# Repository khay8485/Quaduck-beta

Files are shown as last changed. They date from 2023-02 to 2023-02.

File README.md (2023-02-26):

# Quaduck

Hello dear friend of excentric 3D-printers, may I introduce the Quaduck, 
an IDEX Printer with in Z completely independent Toolheads, based on the Voron Switchwire.
The naming originates from a long CAD session, where I started seeing a duck's face on a 
specific part of the printer. Therefore Switchwire meets ZIDEX meets ducks.

The files contain the first version of an assembly manual, but it is missing steps that 
are unchanged from SW or discovered after writing.

CAD is included hence beta, cause other projects needed the data.
Be aware, that I am NOT maintaining this repo on a daily basis, so it might be outdated. 

If you have questions, feel free to ask on discord. Add an # between my github-username.

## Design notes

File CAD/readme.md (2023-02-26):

CAD Version 42, no history but hidden parts of SW-origin

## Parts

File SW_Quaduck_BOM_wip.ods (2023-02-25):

Category | Part | Quantity | Quantity for Quaduck
Frame | 3060 Extrusion – 520mm | 2 | 2
 | 3030 Extrusion – 300mm | 2 | 2
 | 3030 Extrusion – 360mm | 1 | 1
 | 3030 Extrusion – 400mm | 2 | 2
 | 2020 Extrusion – 340mm | 2 | 3
Fasteners | M3 Threaded Insert | 54 | 40
 | M3 T-Nut (For 2020) | 13 | 28
 | M3 T-Nut (For 3030) | 12 | 24
 | M5 T-Nut (For 2020) | 12 | 15
 | M5 T-Nut (For 3030) | 55 | 42
Bearringstacks | M5 1mm Spacer | 19 | 42
TAP Rail | M3 Hexnut | 3 | 4
Frame | M8x16 BHCS | 8 | 8
XZ-Idlers | M5x50 BHCS |  | 4
Keybak, | M5x40 SHCS | 6 | 2
Y-Idler, Xz-blocks, | M5x30 BHCS | 5 | 9
Feet, XZ-Motormounts, | M5x16 BHCS | 12 | 12
Railstopper, XZ-Idler, PDU, Y-Idler, Y-Motor, Deckpanel, YZ-Chainholder, Skirts, XZ-Blocks | M5x10 BHCS | 50 | 40
PDU | M4x8 BHCS | 4 | 3
XZ-Motormounts, | M3x40 SHCS | 7 | 4
XZ-Idlers, Y-Motor, Beplate, E-Fans, XZ-Motormounts | M3x30 SHCS | 28 | 30
 | M3x25 SHCS | 2
 | M3x20 SHCS | 3
 | M3x16 SHCS | 12
Y-Beltholder, | M3x12 SHCS | 12 | 1
Rails, Bedplate, Skirts, X-Cablecover, XZ-Blocks | M3x8 SHCS | 66 | 88
 | M3x6 FHCS | 9
Y-Endstop, X-Endstop | M2x10 Self-tapping Screw | 8 | 6
Bed Fasteners | M3x12 FHCS (SS) | 9 | 9
 | 6x6x3mm Spacer (SS) | 9 | 9
Vibration Management | Rubber Compressor Foot | 4 | 4
Motion | MGN12H Linear Rail – 300mm | 4 | 7
 | GT2 20T Pulley (5mm B, 6mm W) | 3 | 5
 | GT2 Belt (6mm W) - 1500mm | 2 | 4
 | GT2 Belt (6mm W) - 800mm | 1 | 1
 | F695 Bearing | 20 | 42
 | BMG Extruder Components Kit | 1 | 2
Electronics | NEMA17 Motor 17HS15-1504S1 | 3 | 5
 | SPDT KW10 Limit Micro Switch | 2 | 4
 | Omron TL-Q5MC2 - NPN Inductive Probe | 1 | 0
 | Hotend Kit (24V) | 1 | 2
 | 2020 Extrusion – 340mm | 1 | 1-2
 | 40x40x10 Axial Fan (24V) | 1 | 2
 | Moons CSE14HRA1L410A-01 |  | 2
 | Mini 12864 Display | 1 | optional
 | Inlet Power Socket IEC320 C14 | 1 | 1
 | Keystone CAT6 Insert | 1 | optional
 | BTT Octopus with 7 Drivers |  | 1
 | 60x60x20 Axial Fan (24V) | 1 | optional
 | USB Cable A-male B-male | 2
 | RaspberryPi3 B+ | 1 | 1
 | Mean Well LRS-350-24 PSU | 1 | 1
 | Mean Well RS-25-5 PSU | 1 | 0
 | BAT85 Diode | 1 | 0
 | C13 Power Cord | 1 | 1
 | MOSFET Trigger Switch Drive Module | 2 | optional
 | LED Strip 240mm 24v | 2 | optional
Buildplate | Prusa MK3 Y Carrier | 1 | 1
 | Prusa MK52 Heated Bed - 24V | 1 | 1
 | Spring Steel Sheet for Prusa MK52 Bed | 1 | 1
Misc | Key-Bak Super 48 Retractable Keychain | 1 | 2
 | 3M VHB Tape 5952 | 1
 | Loctite Blue Threadlocker Stick | 1
 | 6x3mm Neodymium Magnet | 8 | 4
 | PTFE Tube (4mm OD 2mm ID) - 300mm | 1
Cable Management | 10x11 Cable Chain | 3 | 5
Cables | 16AWG PTFE Cable (10ft total) | 1
 | 20AWG PVC Cable (10ft total) | 1
 | 24AWG PTFE Cable (100ft total) | 1
Panels | 366x270x3 Coroplast Panel | 1
 | 441x270x3 Coroplast Panel | 2
 | 426x360x3 Coroplast Panel | 2
 | 478x170x3 Coroplast Panel | 2
 | 478x360x3 Coroplast Panel | 2
 | 433x183x3 Acrylic Panel | 2
 | 366x250x3 Acrylic Panel | 1
 | 441x250x3 Acrylic Panel | 2

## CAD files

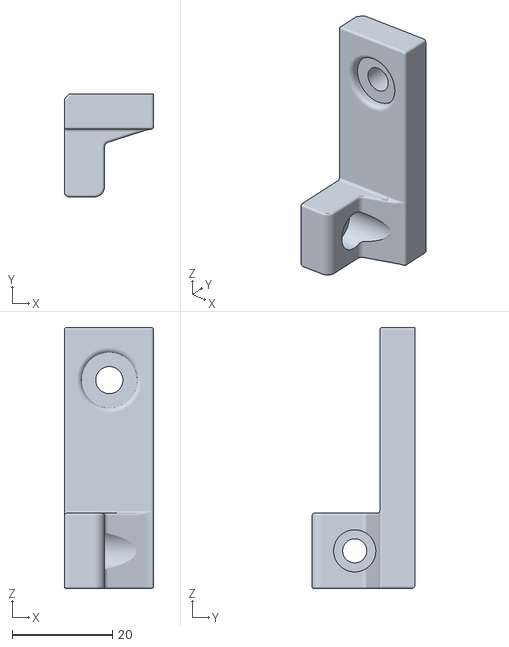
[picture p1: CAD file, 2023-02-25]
Electronics/PS_2020_Mount_M4x6.stl
17.8 x 20.5 x 52.0

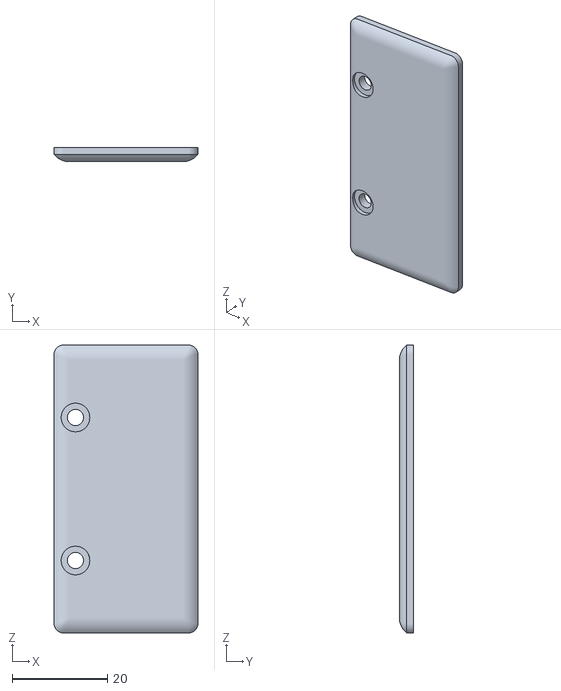
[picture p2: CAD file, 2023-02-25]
Skirts/endcapducky_mmu.stl
30.2 x 3.00 x 60.4

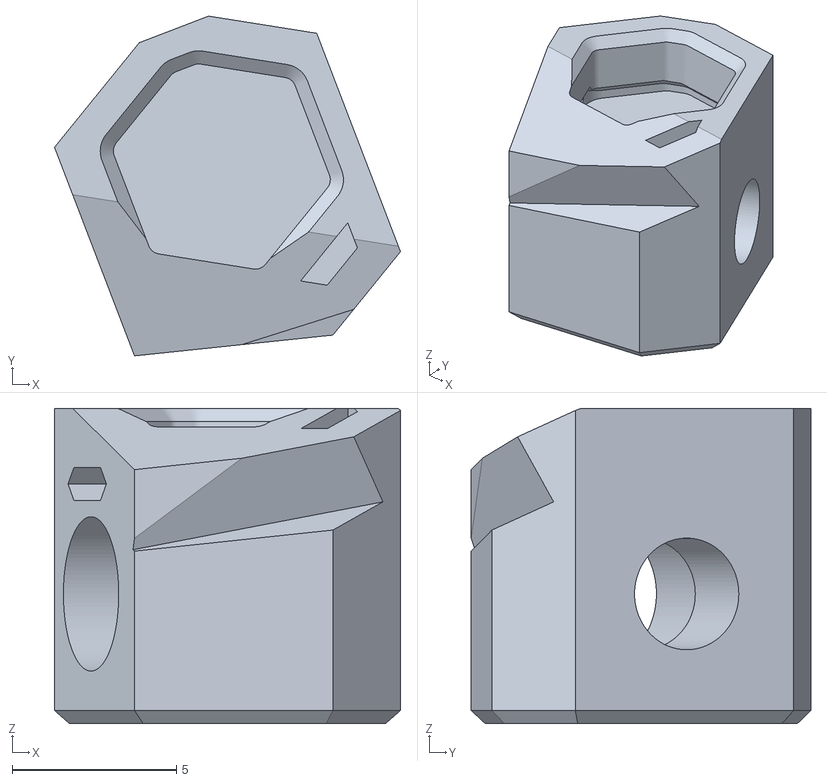
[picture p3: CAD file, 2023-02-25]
x2/Carriage/tippi_mag_right.stl
10.5 x 10.3 x 9.60

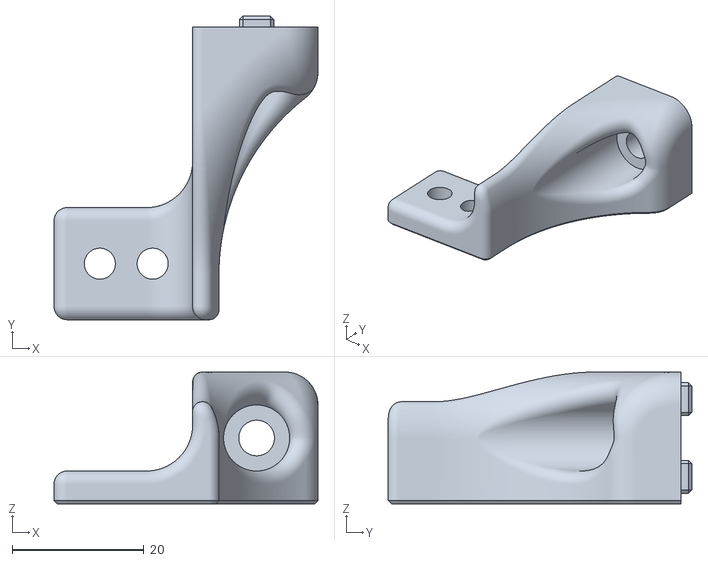
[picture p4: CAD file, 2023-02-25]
x2/X-Axis/z_chain_x_mount.stl
40.0 x 46.0 x 20.0

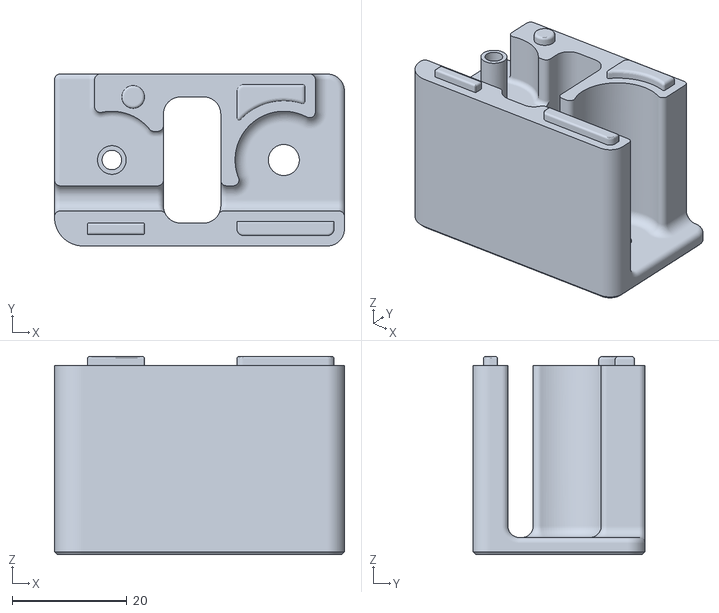
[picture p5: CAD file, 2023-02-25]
x2/XZ-System/upper_idler_right_a.stl
50.6 x 30.0 x 34.6

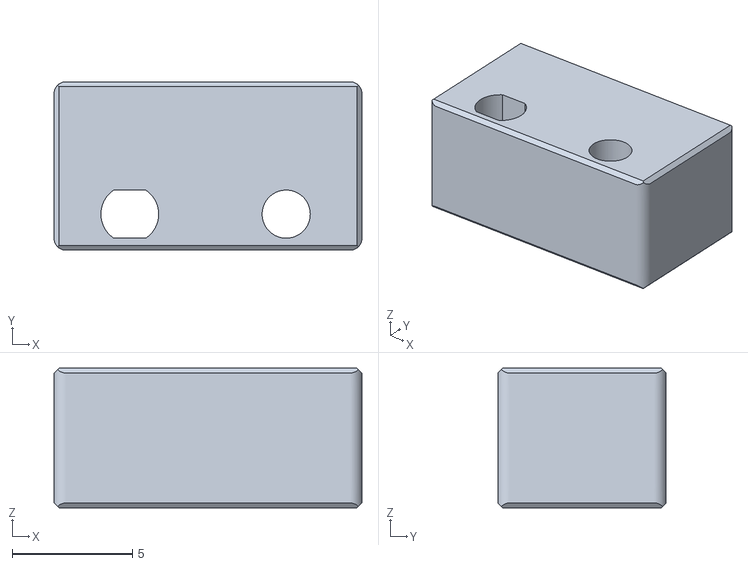
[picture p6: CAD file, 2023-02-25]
Y-Axis/[a]_dummy_microswitch.stl
12.8 x 7.00 x 5.80

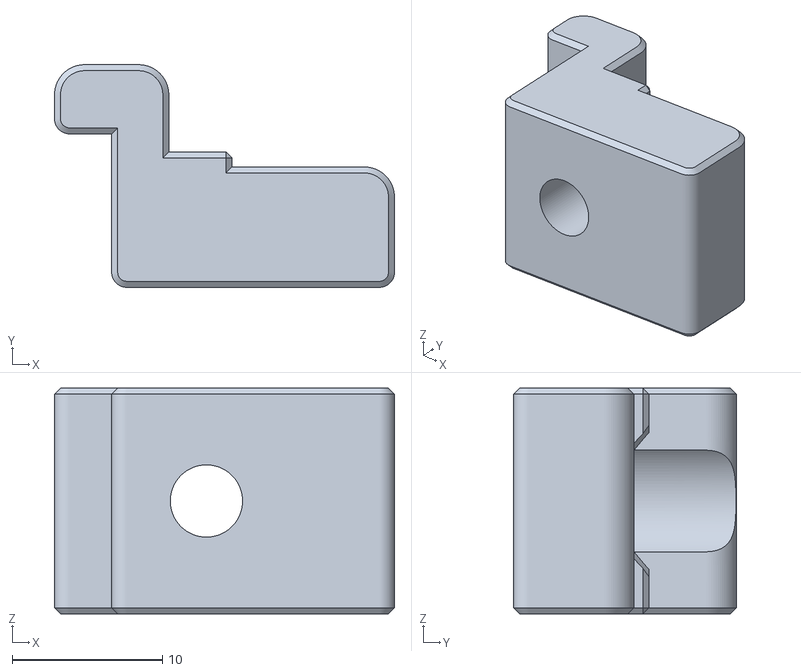
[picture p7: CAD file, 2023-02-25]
Electronics/PS_3030_Mount_x2.stl
22.6 x 14.8 x 15.0

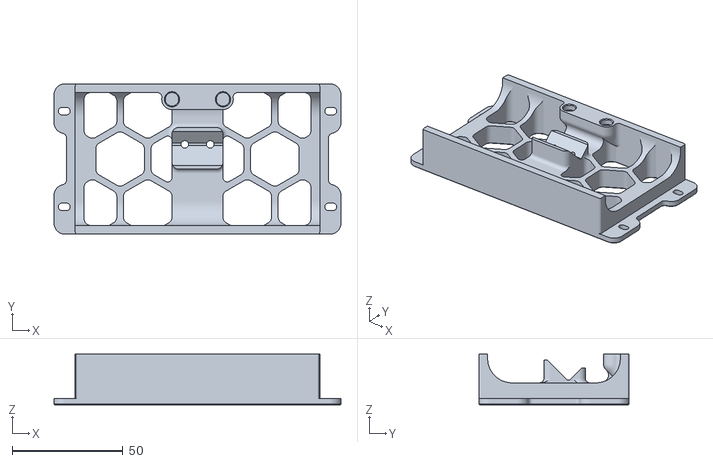
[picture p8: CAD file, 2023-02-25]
Skirts/grill_front_middle.stl
129.8 x 68.0 x 23.0

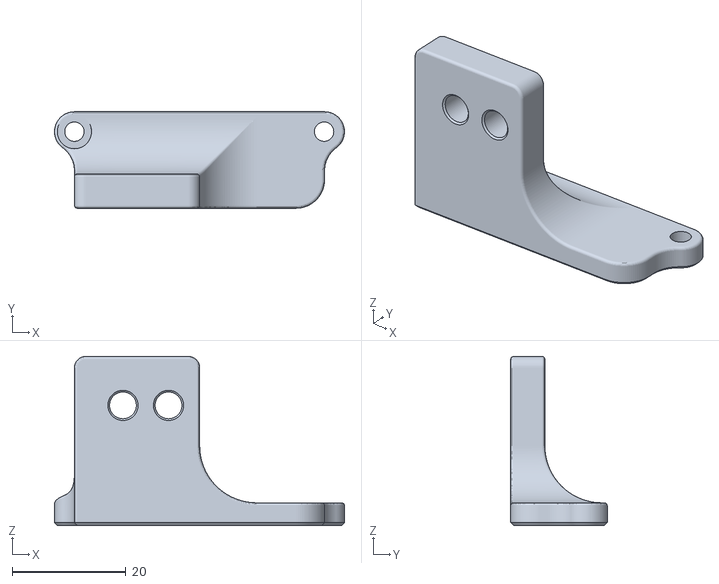
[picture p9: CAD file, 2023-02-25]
x2/Carriage/x_carriage_chainmount_rev1.stl
50.9 x 16.9 x 29.7

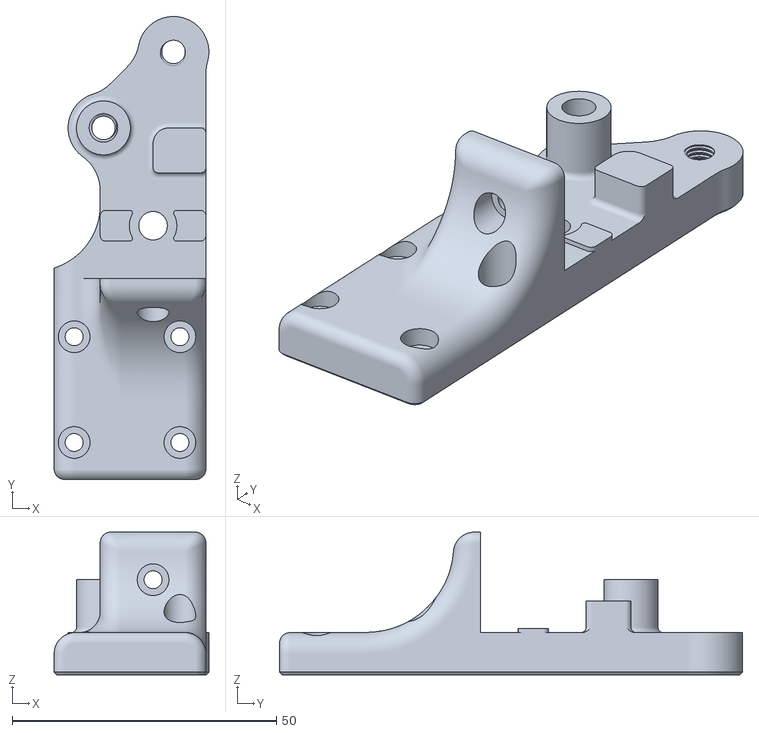
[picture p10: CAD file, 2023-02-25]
x2/X-Axis/(a) xz_block_right_ducky_V2.stl
29.3 x 87.6 x 27.0

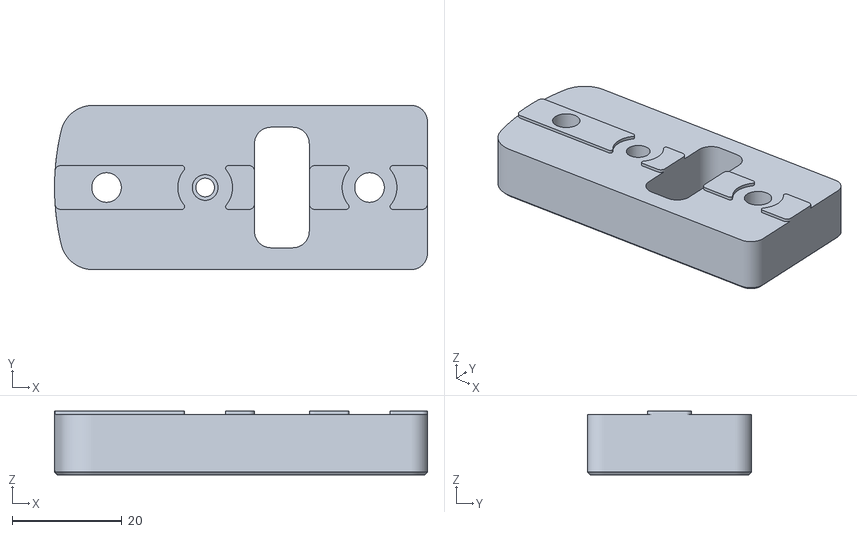
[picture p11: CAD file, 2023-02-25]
x2/XZ-System/(a) upper_idler_right_b.stl
68.1 x 30.0 x 11.6

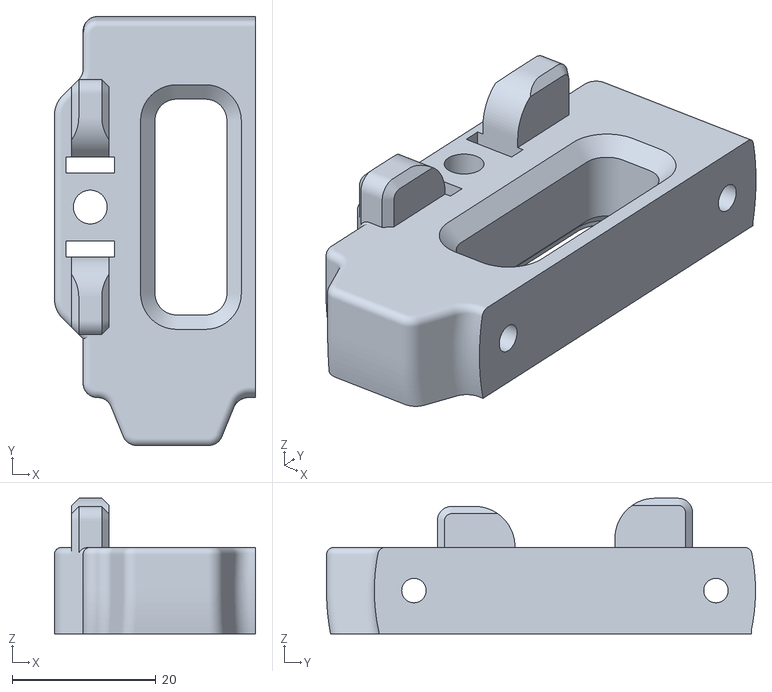
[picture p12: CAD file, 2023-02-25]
Y-Axis/y_belt_anchor_sensorless.stl
28.0 x 59.7 x 18.8

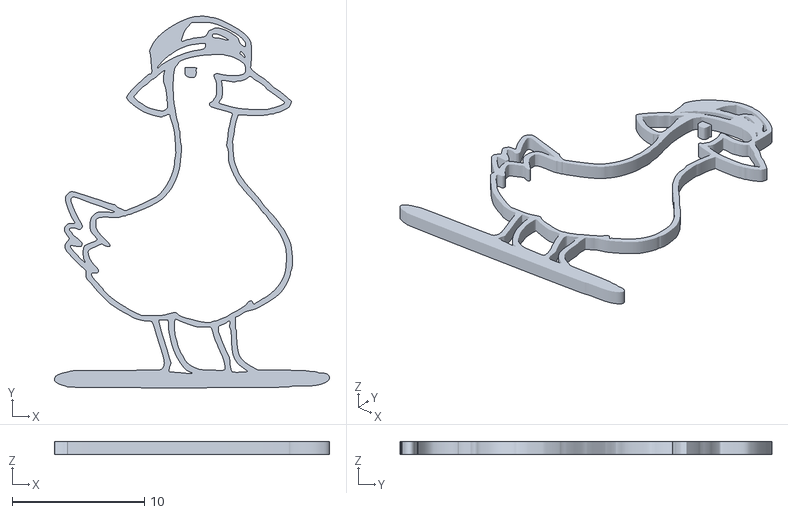
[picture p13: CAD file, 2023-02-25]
Skirts/endcapducky_single.stl
20.8 x 28.1 x 1.00

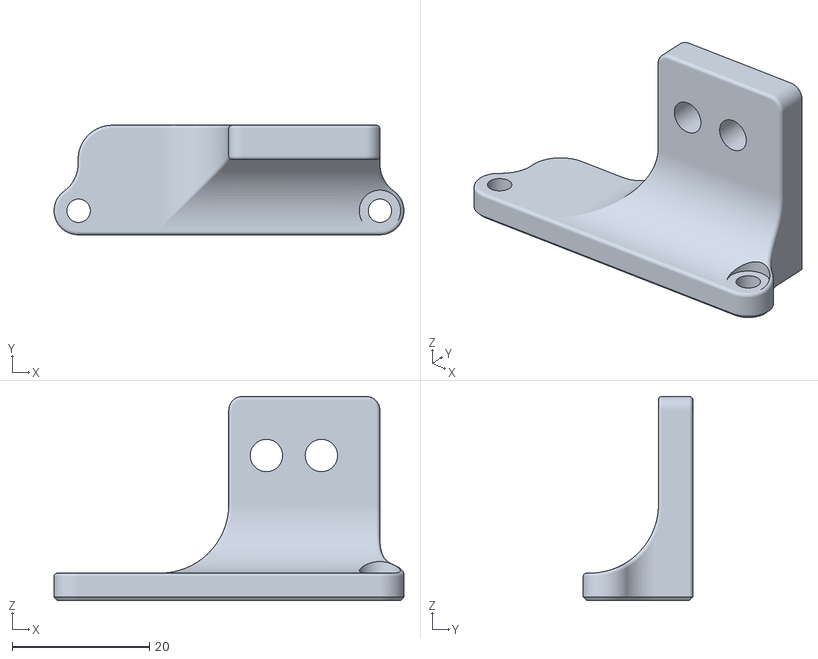
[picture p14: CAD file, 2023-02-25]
x2/Carriage/x_carriage_chainmount.stl
50.9 x 15.9 x 29.7

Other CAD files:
Electronics/PS_2020_Mount.stl
x2/X-Axis/xz_block_left_front.stl
x2/XZ-System/x_motor_mount_a.stl
Y-Axis/y_idler_upper.stl
Electronics/PS_3030_Mount_M4x6 x2.stl
Electronics/octopus_mount.stl
Electronics/raspberry_pi_mount.stl
Skirts/12mm printed spacer x2-4.stl
Skirts/[a]_grill_endcap_d_x2.stl
Skirts/[a]_grill_endcap_x2.stl
Skirts/grill_front_x2.stl
Skirts/grill_rear_left_inlet.stl
Skirts/grill_rear_middle.stl
Skirts/grill_rear_right.stl
Y-Axis/(a) zy_chain_frame_mount_x2.stl
Y-Axis/[a]_y_belt_clip.stl
Y-Axis/[a]_y_chain_bed_mount_generic.stl
Y-Axis/[a]_y_chain_bed_mount_igus.stl
Y-Axis/heatbed_terminals_cover.stl
Y-Axis/y_belt_anchor.stl
Y-Axis/y_carriage_drill_guide.stl
Y-Axis/y_idler_lower.stl
Y-Axis/y_motor_mount_a.stl
Y-Axis/y_motor_mount_b.stl
x2/Carriage/(a) xz_belt_clip_x2.stl
x2/Carriage/sb_strain_relief_spacer_x2.stl
x2/Carriage/tippi_mag_left.stl
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

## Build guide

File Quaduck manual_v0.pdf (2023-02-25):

# Quaduck

## Voron Switchwire Double X-Gantry Version/Mod

### Hello dear friend of excentric 3D-printers, may I introduce the Quaduck, an IDEX Printer with in Z completely independent

Toolheads, based on the Voron Switchwire.

### The naming originates from a long CAD session, where I started seeing a duck's face on a specific part of the printer. Can you see it? Well, then you have to build it. ;-)

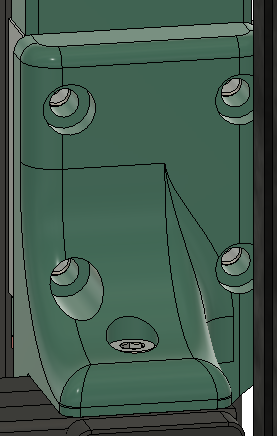
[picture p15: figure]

### nat nat

### It combines: - ZIDEX 3D-Printer idea - Switchwire - TAP - Mini Stealthburner - Ducks

## XZ-Motionsystem

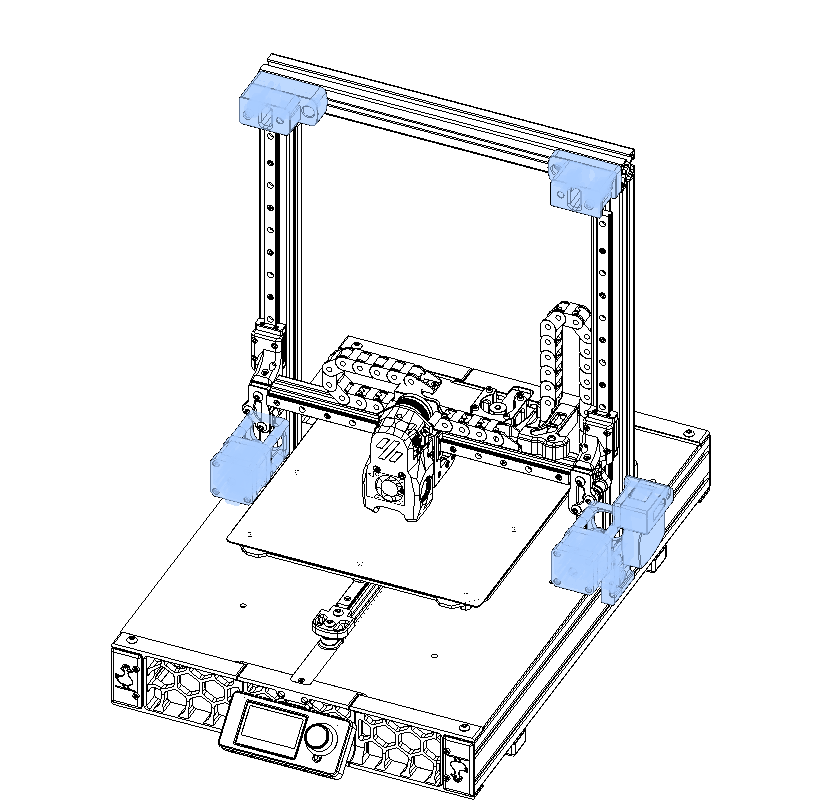
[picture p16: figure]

Rudimentary Build Manual for Tool0-Side of the Duck.

### You will the printed parts from: - X2 / XZ-System

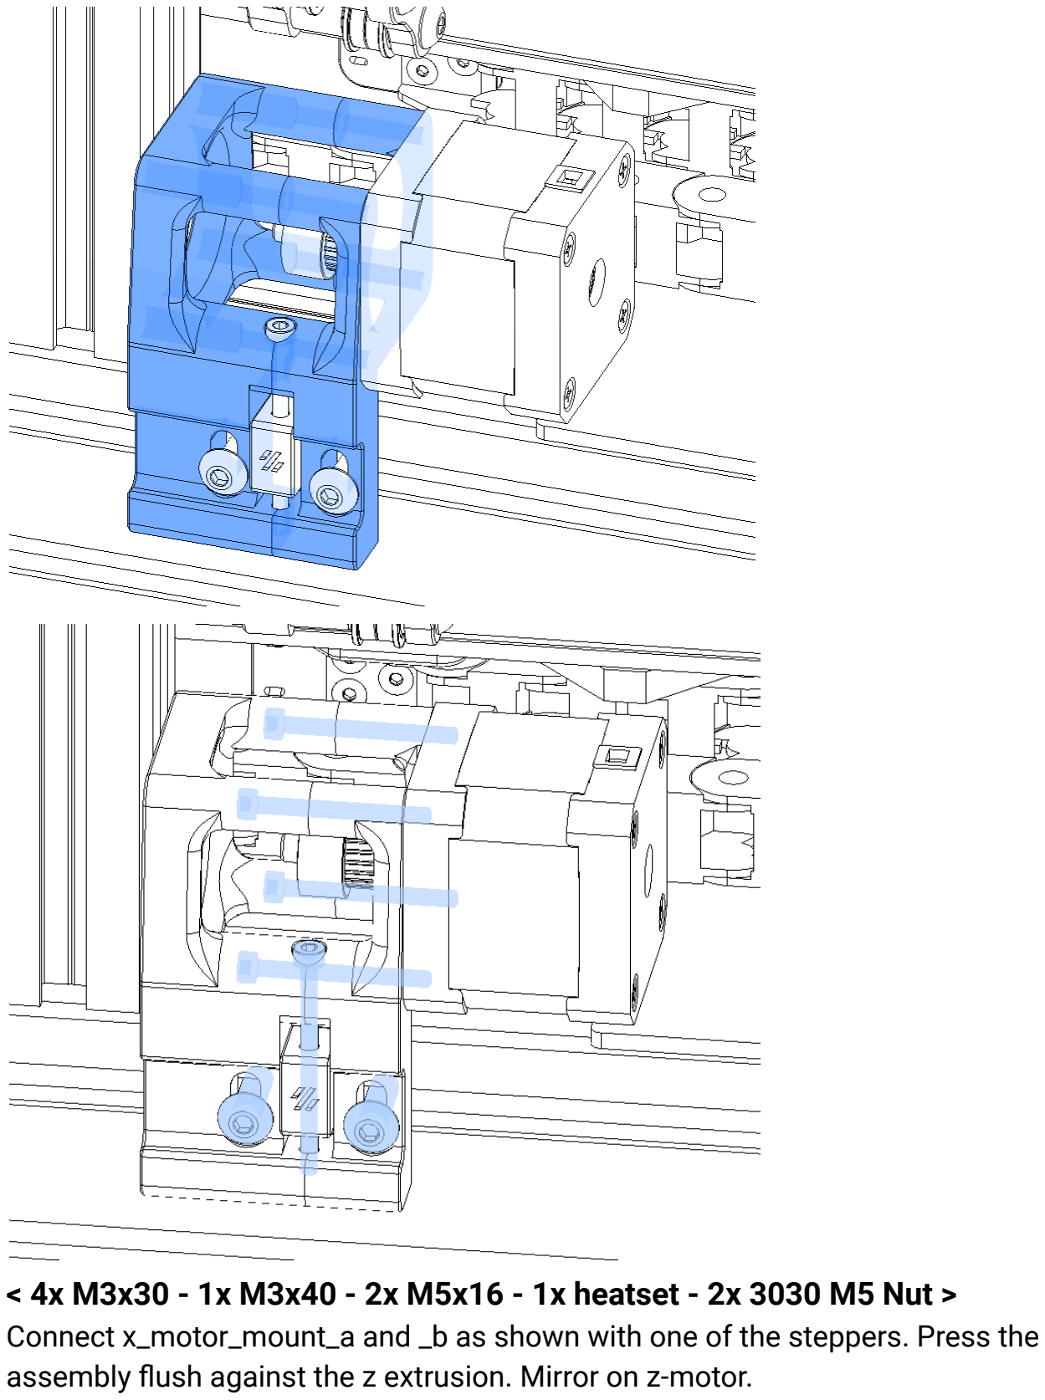
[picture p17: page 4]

< 4x M3x30 - 1x M3x40 - 2x M5x16 - 1x heatset - 2x 3030 M5 Nut > Connect x_motor_mount_a and _b as shown with one of the steppers. Press the assembly flush against the z extrusion. Mirror on z-motor.

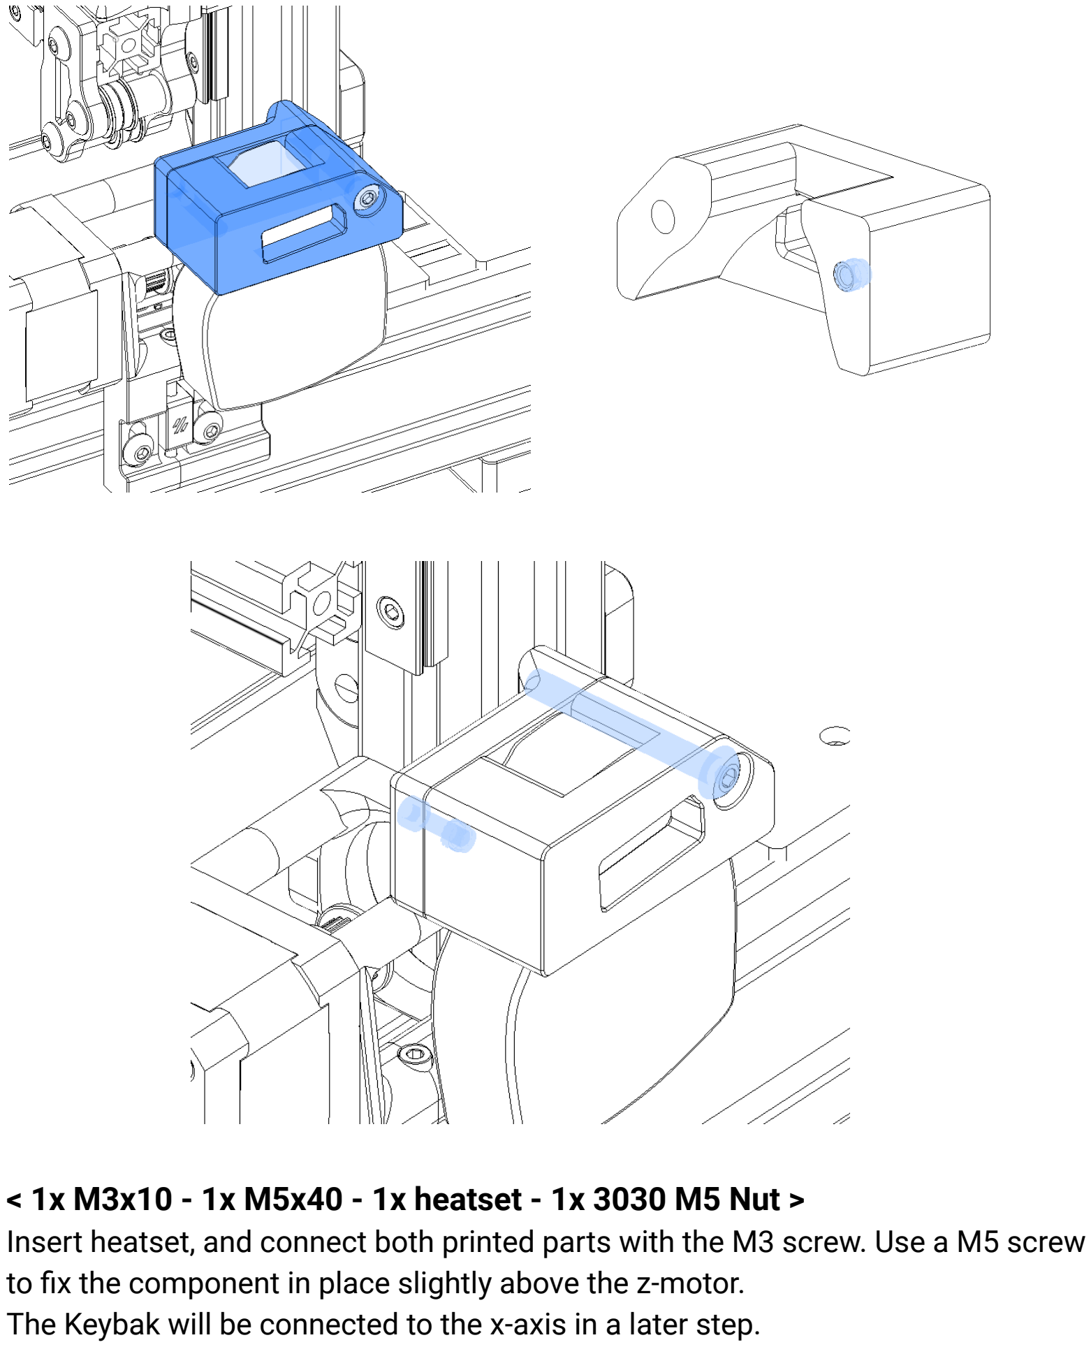
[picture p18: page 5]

< 1x M3x10 - 1x M5x40 - 1x heatset - 1x 3030 M5 Nut >
Insert heatset, and connect both printed parts with the M3 screw. Use a M5 screw to fix the component in place slightly above the z-motor.
The Keybak will be connected to the x-axis in a later step.

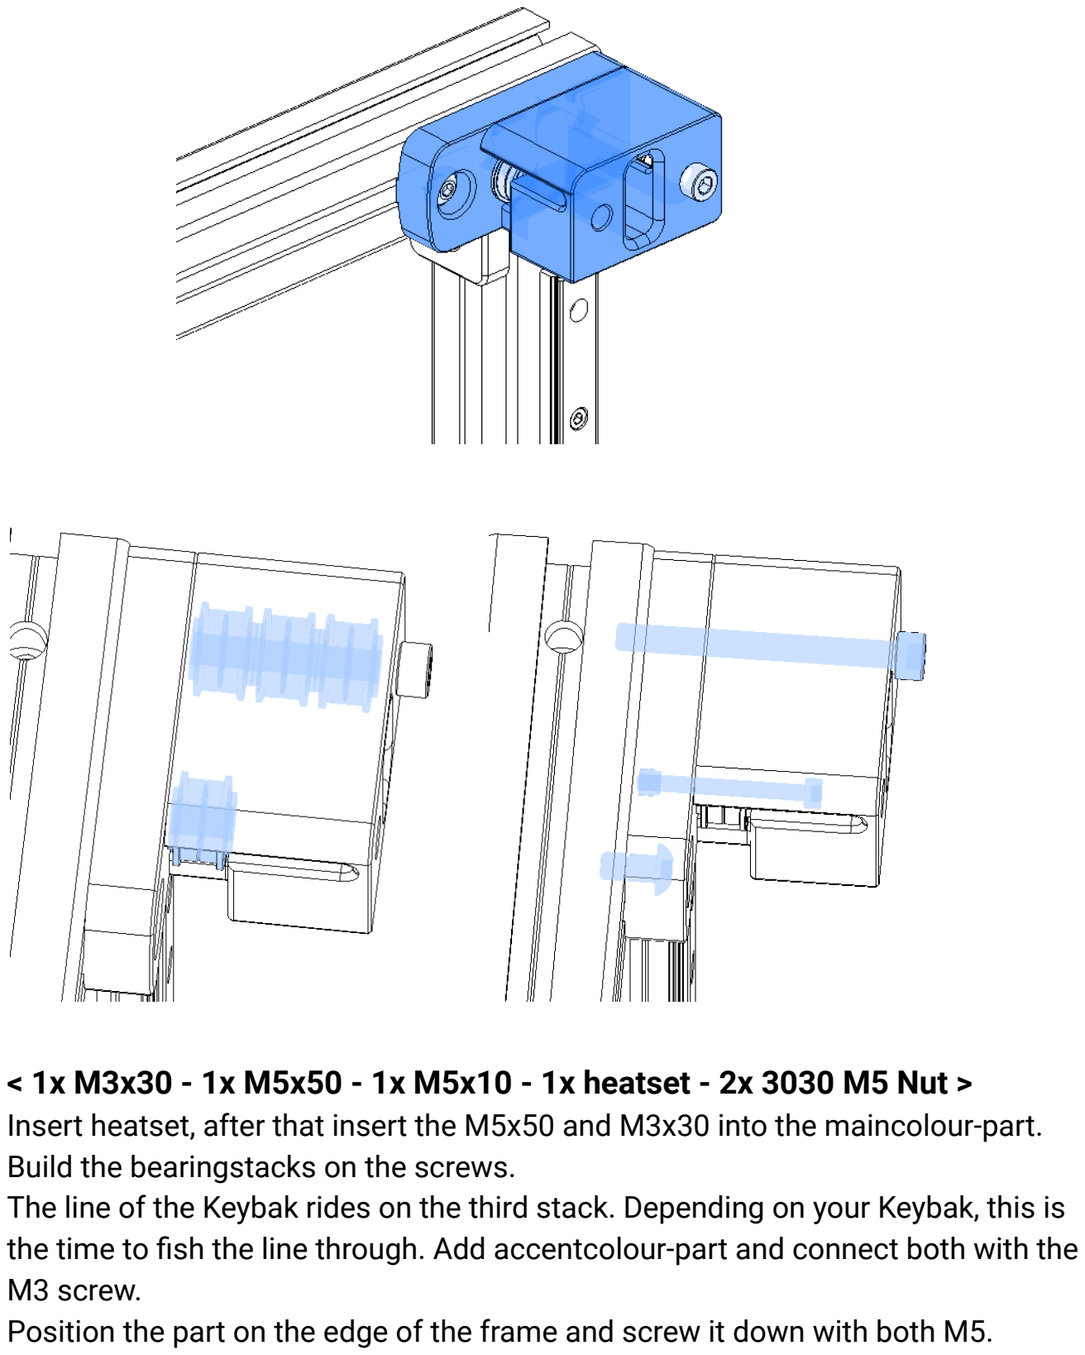
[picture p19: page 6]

< 1x M3x30 - 1x M5x50 - 1x M5x10 - 1x heatset - 2x 3030 M5 Nut > Insert heatset, after that insert the M5x50 and M3x30 into the maincolour-part. Build the bearingstacks on the screws.
The line of the Keybak rides on the third stack. Depending on your Keybak, this is the time to fish the line through. Add accentcolour-part and connect both with the M3 screw.
Position the part on the edge of the frame and screw it down with both M5.

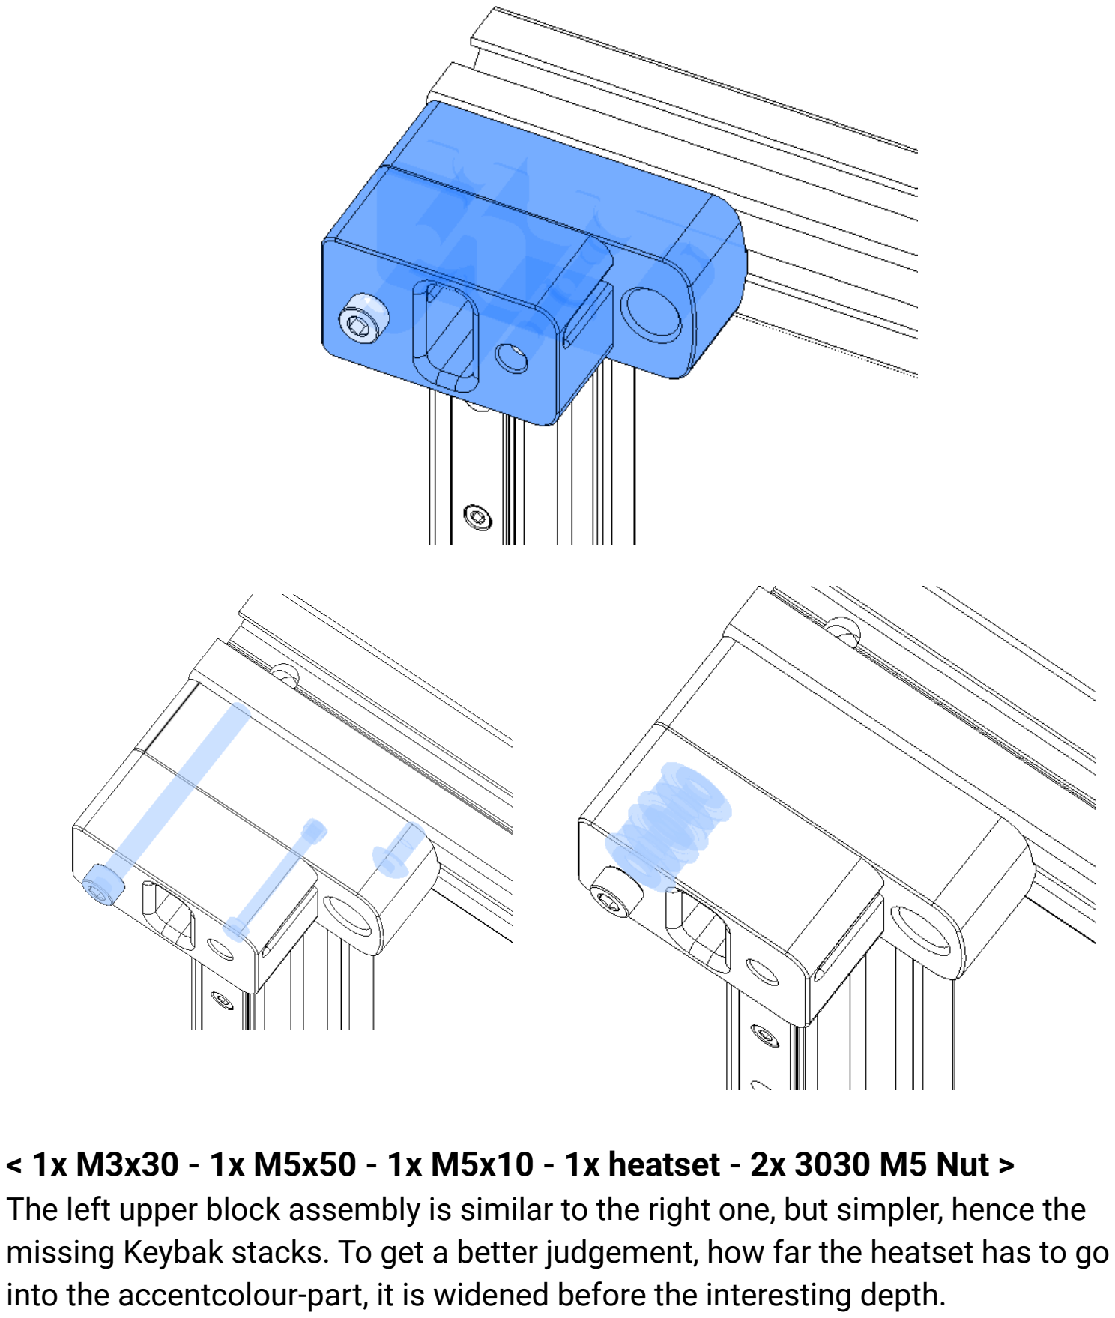
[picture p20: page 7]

< 1x M3x30 - 1x M5x50 - 1x M5x10 - 1x heatset - 2x 3030 M5 Nut >
The left upper block assembly is similar to the right one, but simpler, hence the missing Keybak stacks. To get a better judgement, how far the heatset has to go into the accentcolour-part, it is widened before the interesting depth.

## X-Carrier - TAP - Toolhead

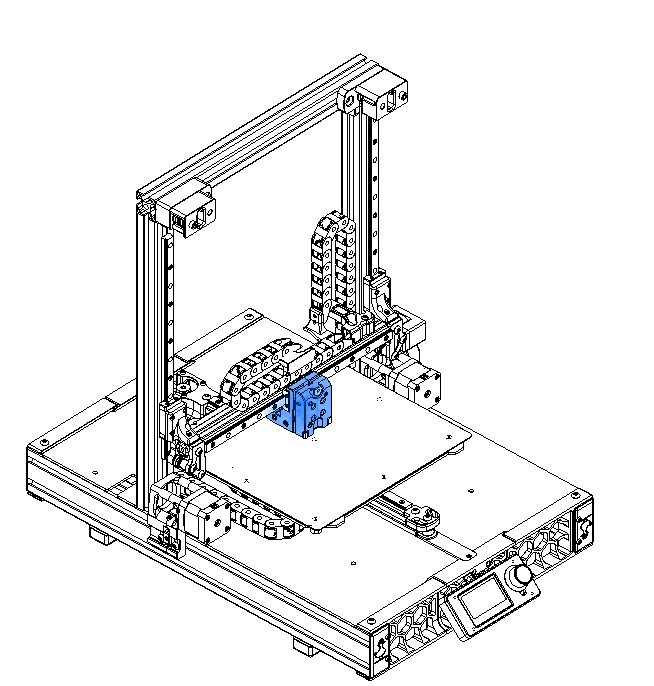
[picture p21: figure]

### You will the printed parts from: - X2 / Carriage

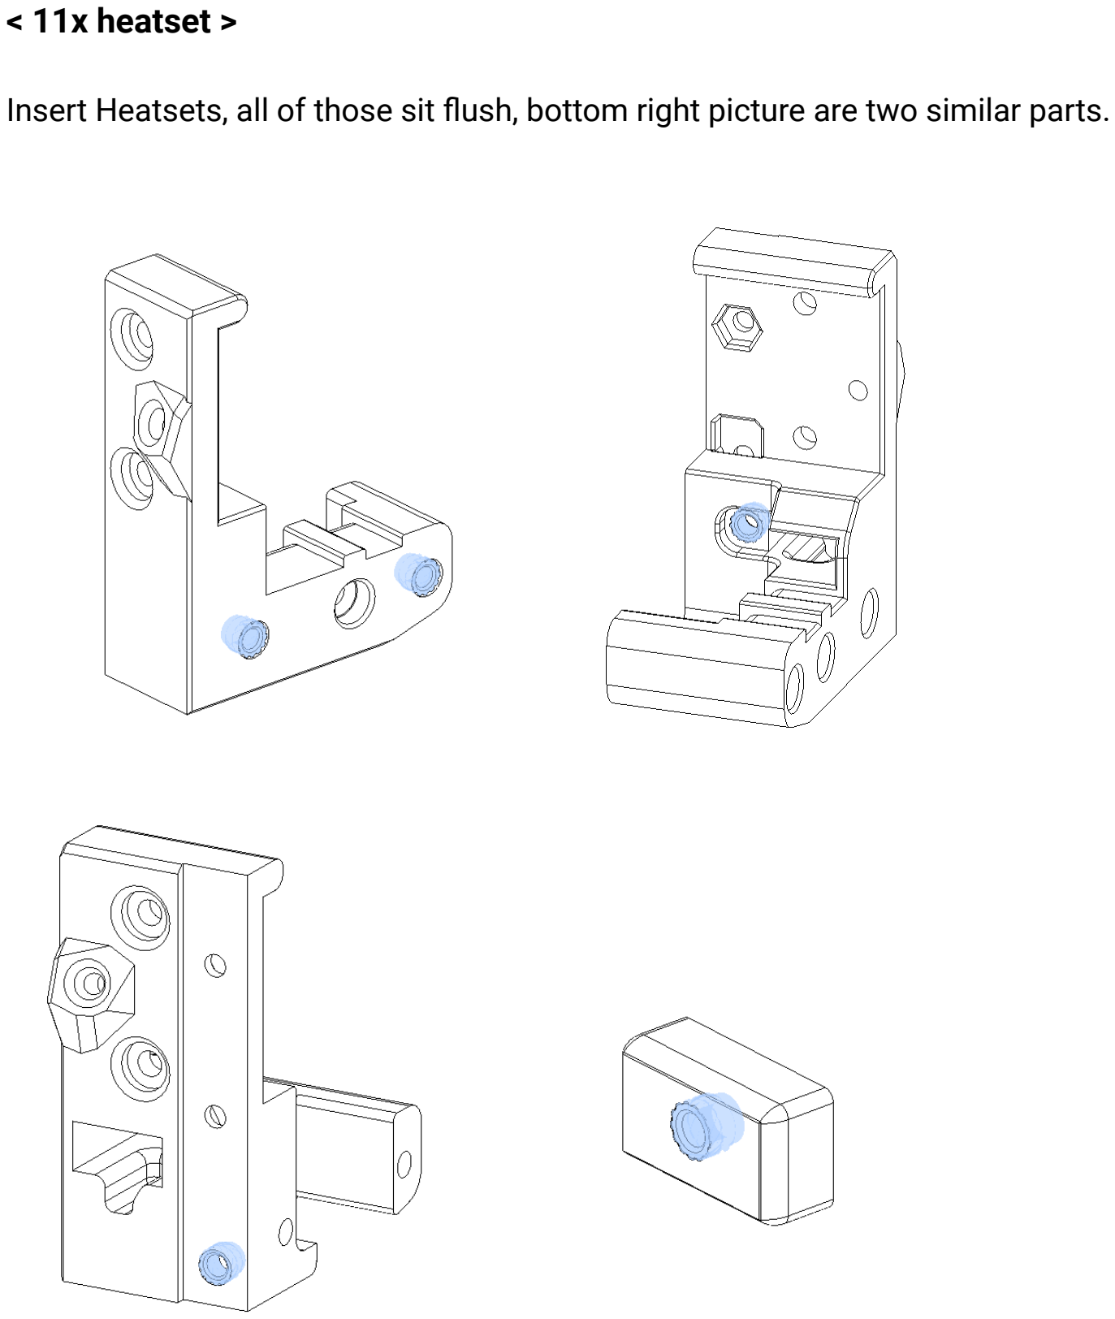
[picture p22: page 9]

< 11x heatset >

Insert Heatsets, all of those sit flush, bottom right picture are two similar parts.

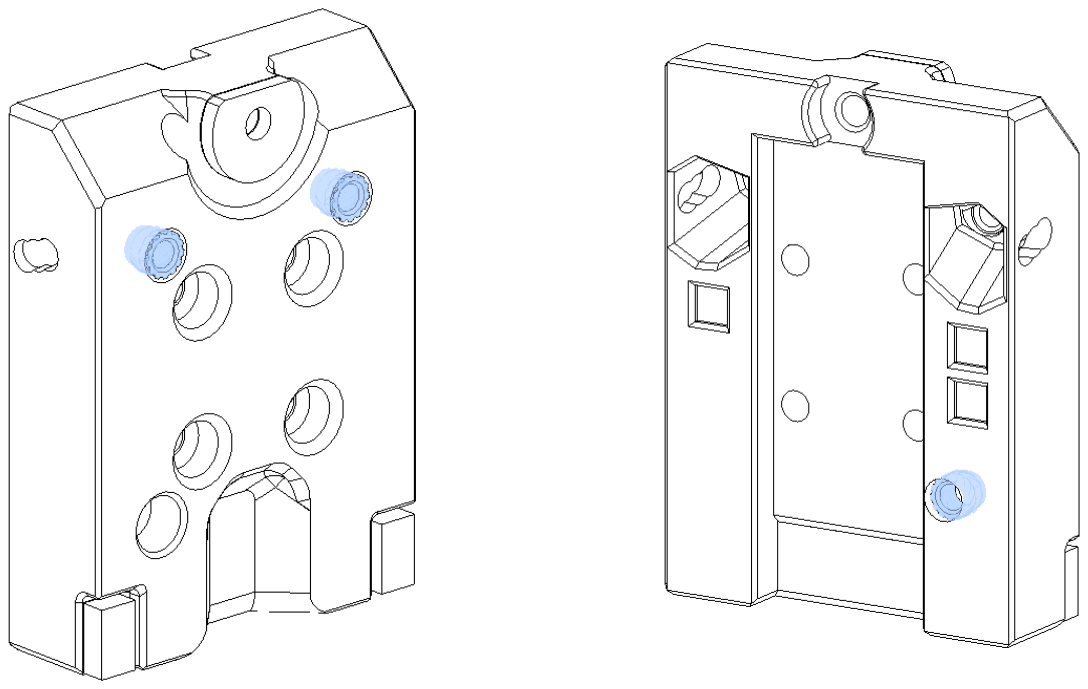
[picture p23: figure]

You can remove the build in supports on this part, maybe the round one needs some conviction with a small flathead screwdriver.

Not shown: the two magnet holder pieces, which each get a heatset too.

< 2x M3x40 - 1x M3x6 - 2x M3 Hex nuts >
Connect both parts and insert the Hex nuts. Add the wired TAP-Sensor.
If you have one with Screw-Terminals on both side, use your flush cutter to get rid of one.

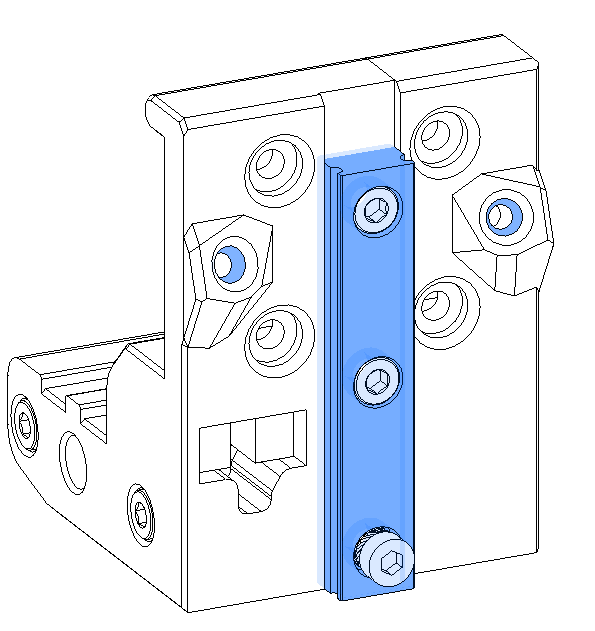
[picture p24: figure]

< 2x M3x6 FHCS - 2x M3x6 - 1x M3x12 - 1x heatset >
Screw the magnetic M3x6 into the elevated parts. Add the TAP MGN9 Rail, use a heatset on the lowest screw. It is a third restingpoint for the toolhead.

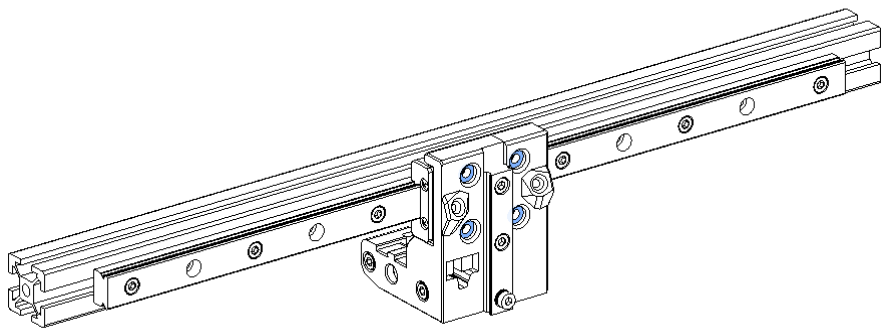
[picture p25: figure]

< 4x M3x8 BHCS >
At this point, you need to mount the carriage onto the x-rail. The handling of this situation will get a bit tricky.

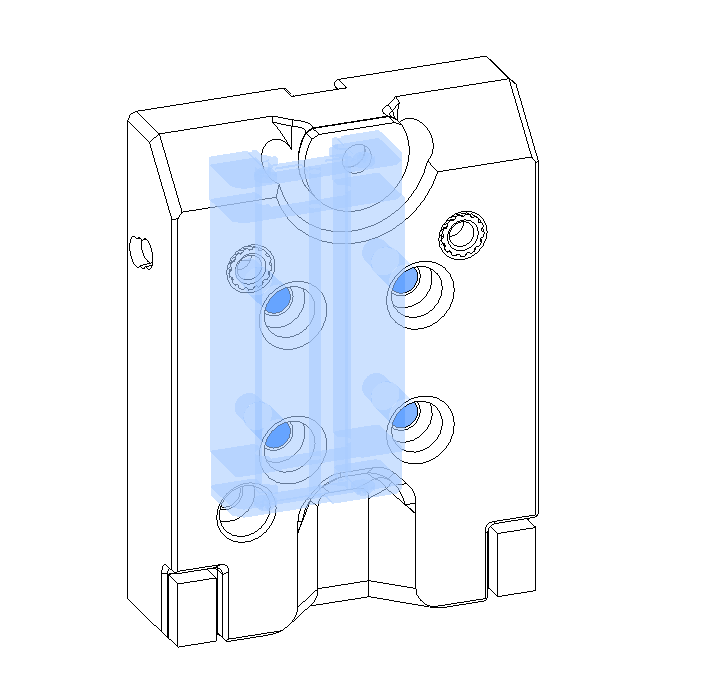
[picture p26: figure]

< 4x M3x8 >
Screw the TAP MGN9 block to the carriage front. Extreme caution when handling this part in the future, as those little balls can get lost easily.

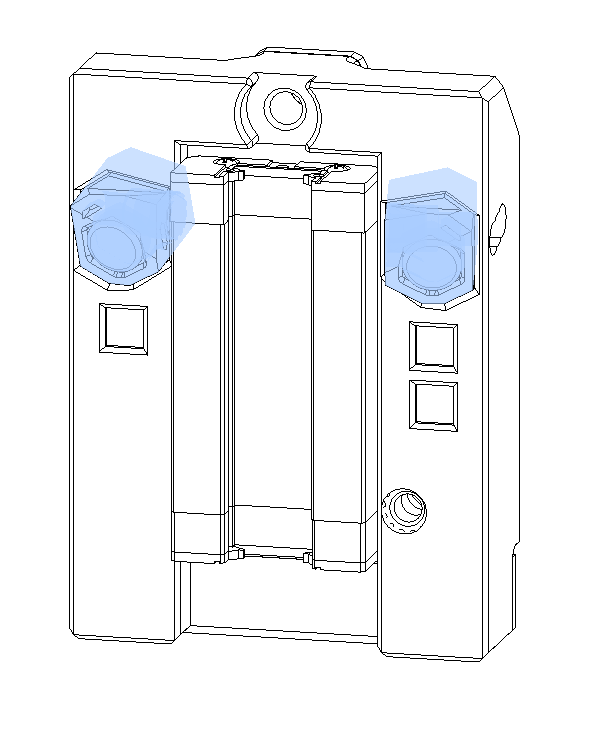
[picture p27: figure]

< 2x M3x10 BHCS - 2 M3 washer >
The magnet holder thingies are marked with dots, the part has similar markings to help you find the right spot for them. Push them all the way in, check loose fit and tack them lightly in place with the screws.

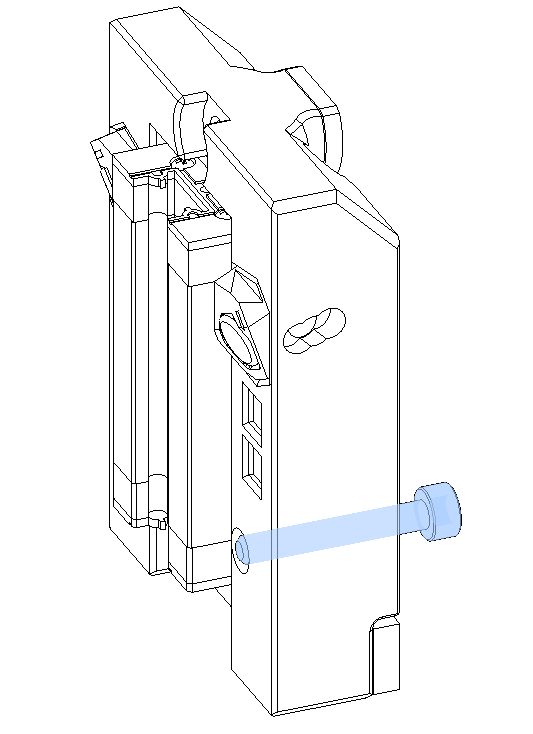
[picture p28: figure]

< 1x M3x20 >
Add the M3x20 as shown. Don’t overshoot the part! This screw will be the trigger for the TAP-Sensor.

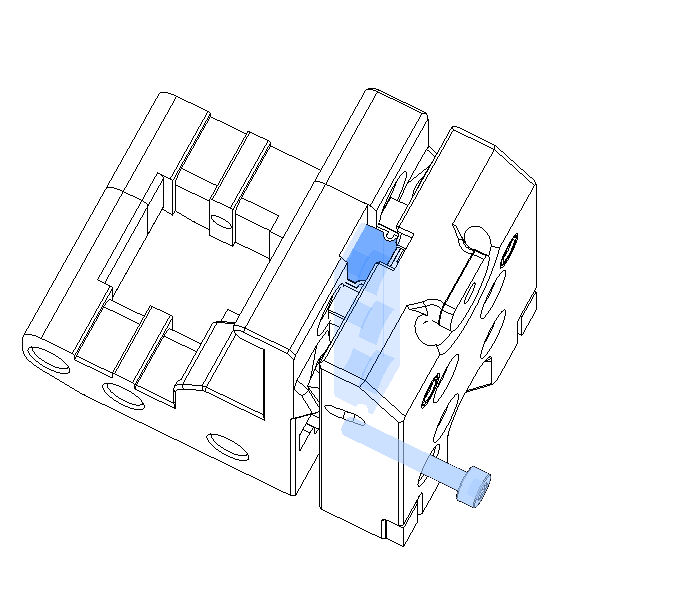
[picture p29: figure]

Gently slide the Carriage front on the MGN9 TAP-Rail. Be cautious, you don’t want to lose any balls out of the block. Slide it all the way down and hold the parts tight in one hand. Screw the M3x20 all the way in. The screw will make sure the carriage-front will not fall off.

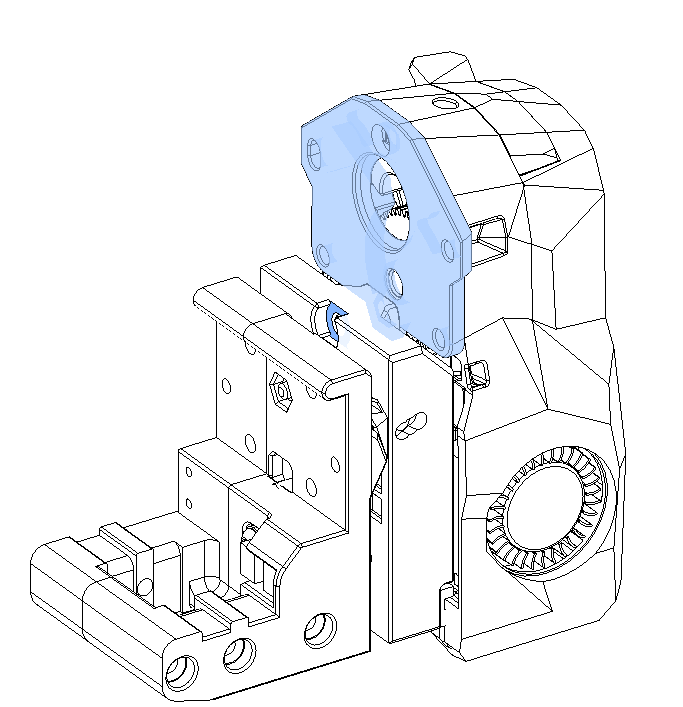
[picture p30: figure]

< 1x M3x12 - 2x M3x35 >
Build the Mini SB Toolhead to the part where you would add the motor. At this stage, connect the Toolhead to the carriage. It will get screwed in on three different spots. To reach the marked one on the picture, gently push up the carriage front. The other two are screwed in from the front.

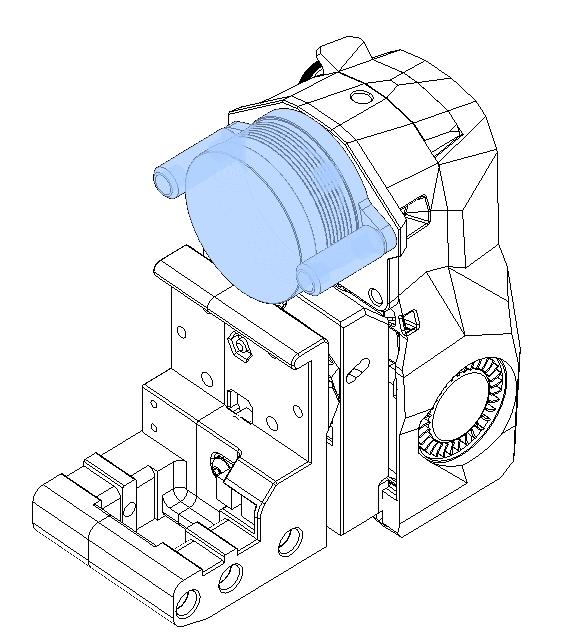
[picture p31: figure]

< 2x M3x10 - 4x heatsets >
Add the stepper motor and strain relief spacers as stated in the Mini-SB manual.

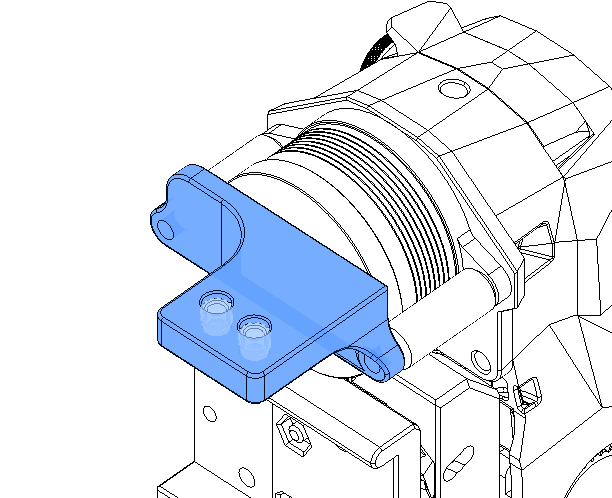
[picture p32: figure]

< 2x M3x8 - 2x heatsets >
The last part is the carriage chainmount. It has another two heatsets and gets screwed in place with two M3x8s.

## X-Axis & more Chainmounts

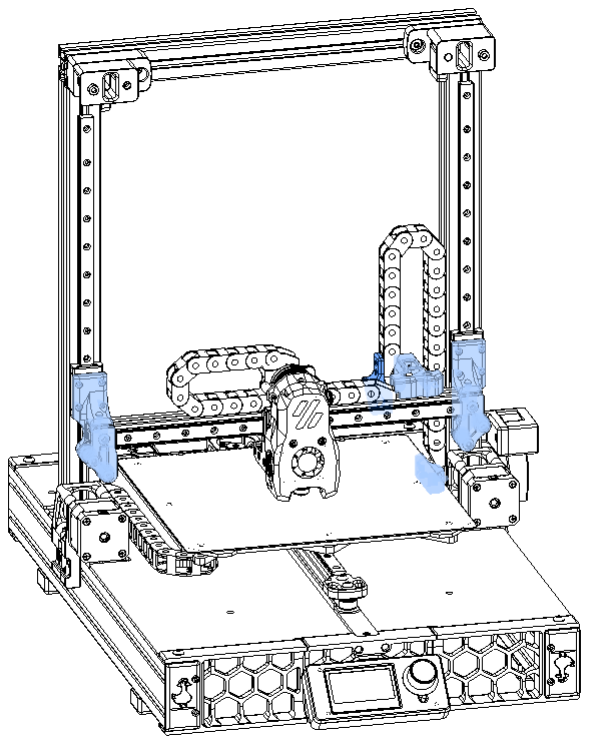
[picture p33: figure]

### You will the printed parts from: - X2 / X-Axis

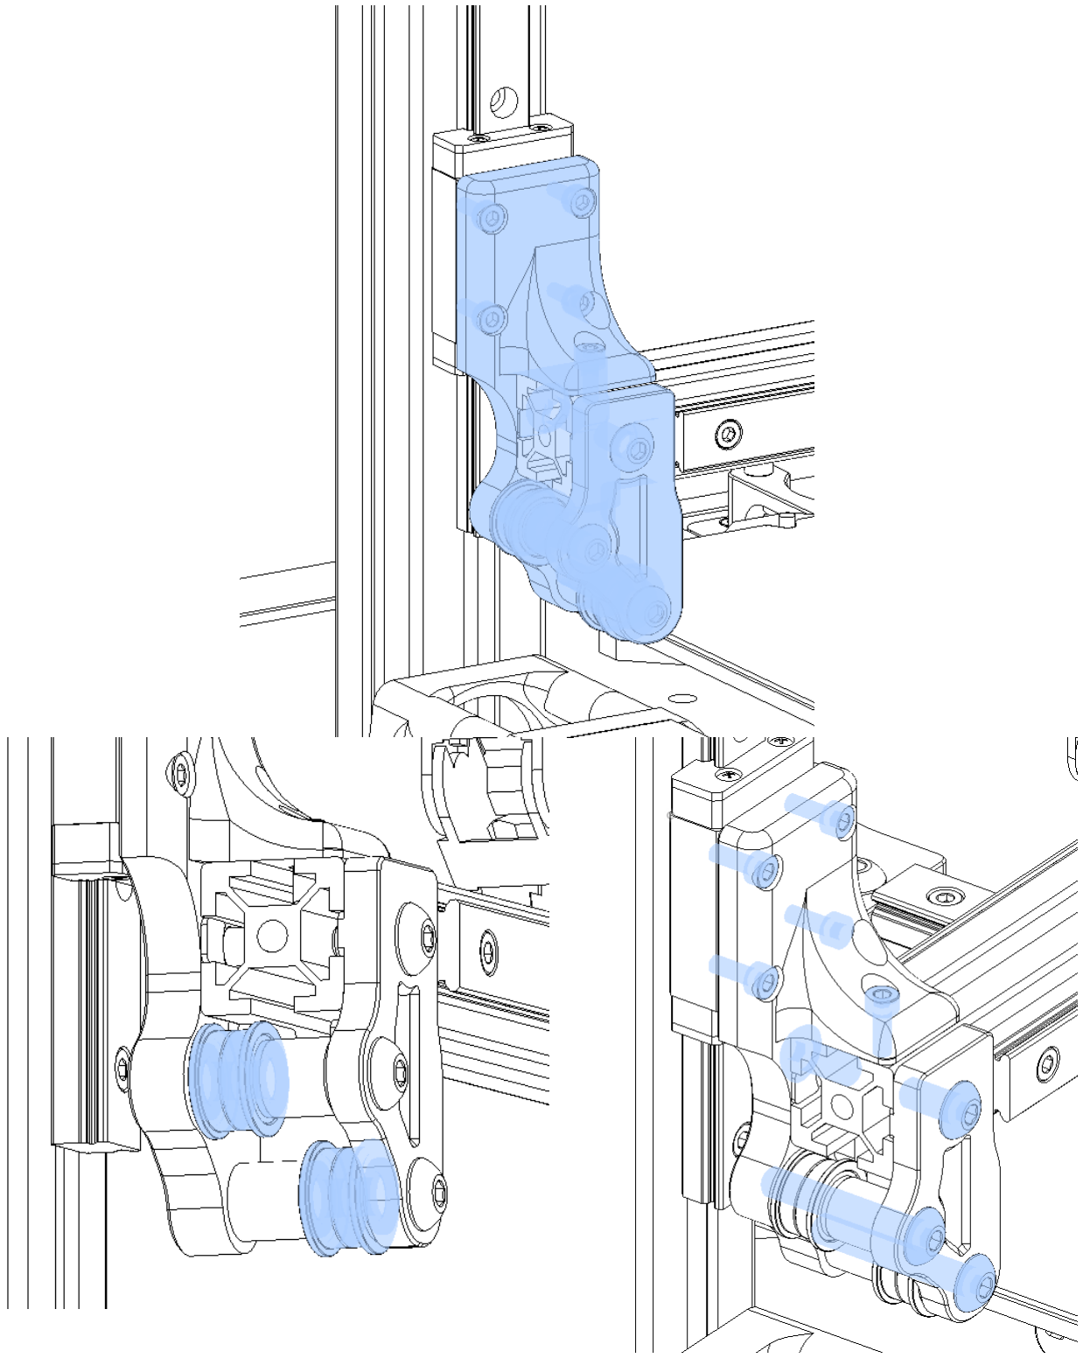
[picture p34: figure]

< 5x M3x8 - 2x M5x30 - 2x M5x10 -
2x 2020 M5 Nut - 1x 2020 M3 Nut > Ducky-part will snap onto 2020 extrusion, position is right on the edge of the extrusion. One bearingstack on each M5x30, those will screw into plastic, do not overtighten.

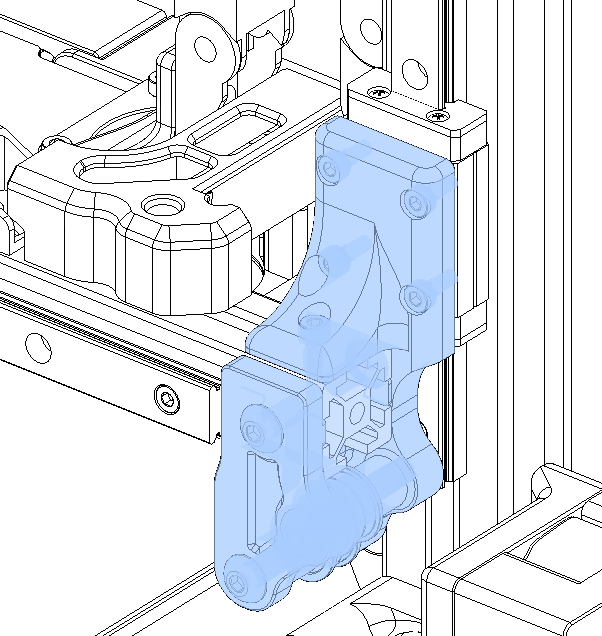
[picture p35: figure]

< 5x M3x8 - 2x M5x30 - 2x M5x10 - 2x 2020 M5 Nut - 1x 2020 M3 Nut > Identical parts and mounting as on the other side. Part sits flush on the end of the extrusion.

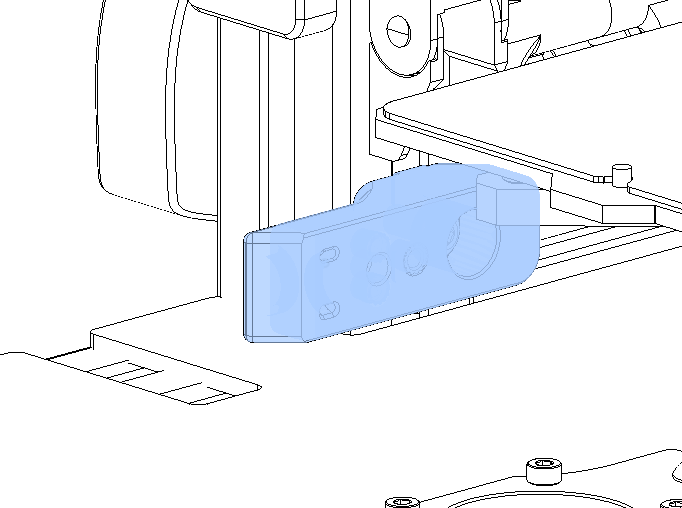
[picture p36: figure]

< 1x M5x10 - 1x 3030 M5 Nut - (2x heatset inserts) >
This part is used for wire management on this side of the printer. There are two anchors for zip ties.
You should have two of this part, the other one is used as y-chain-mount and for wire management of Tool1. The heatsets are not used to this state, could be used for different mods, like a cam-mount.

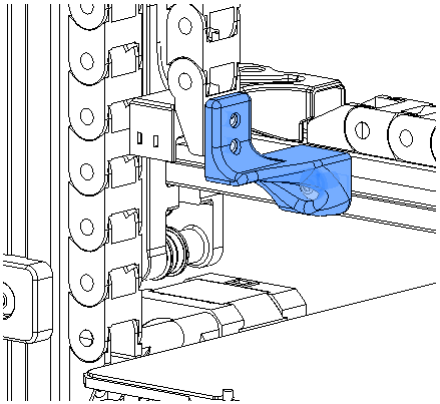
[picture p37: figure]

< 2x M3x6 1x M5x10 - 1x 2020 M5 Nut - 2x heatsets >
This is the upper anchor of the z-cablechain. That part is sketched for IGUS. There are two heatsets and M3 BHCS needed, to connect the cablechain. When using a generic chain, just connect it with one BHCS. It is screwed on the backside of x-axis as far on the “chainside” as possible.

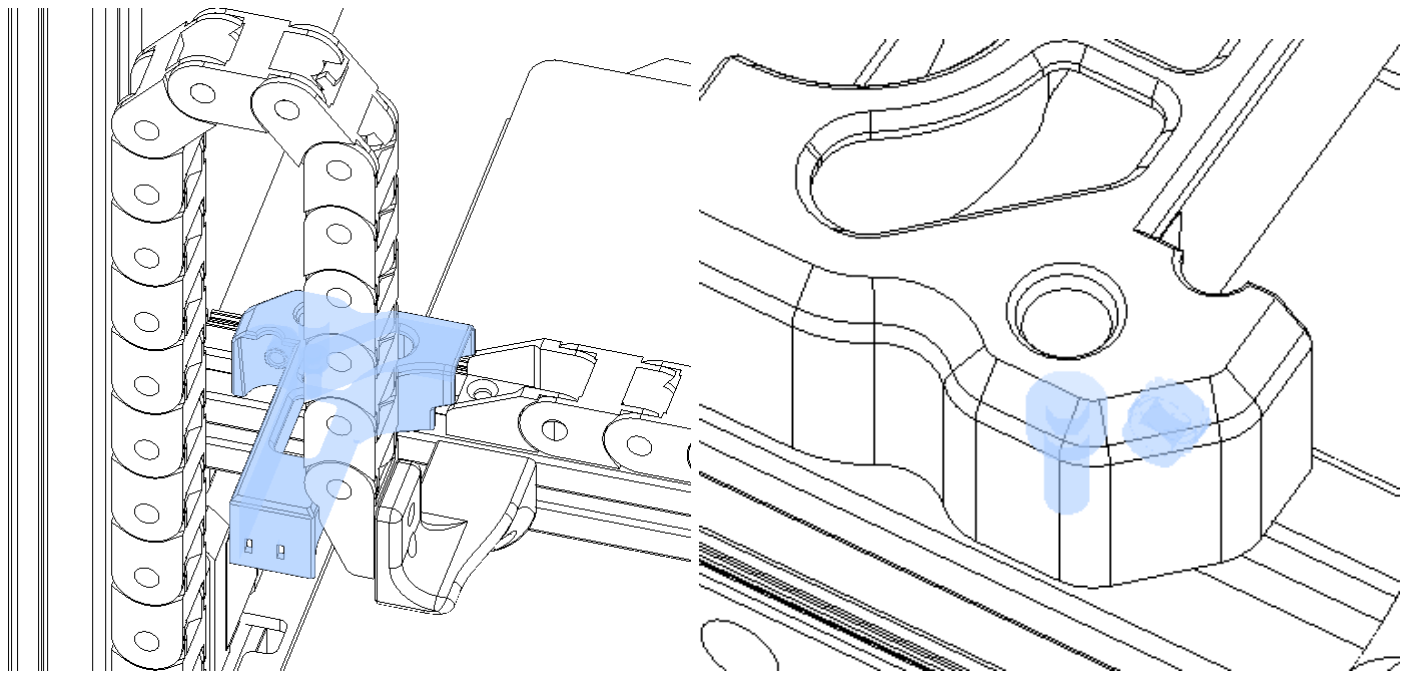
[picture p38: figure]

< 2x M3x8 - 1x 2020 M3 Nut - 1x heatset >
That wonderful, disturbing part is used to get the wires from z-cablechain to x-cablechain without floating in the air. On top of that, the Keybak will be connected to this part, to do its thing. Those funny holes on the backside, give you the opportunity to add another zip tie.
